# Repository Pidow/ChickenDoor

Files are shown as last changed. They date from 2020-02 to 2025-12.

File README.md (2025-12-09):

# ChickenDoor

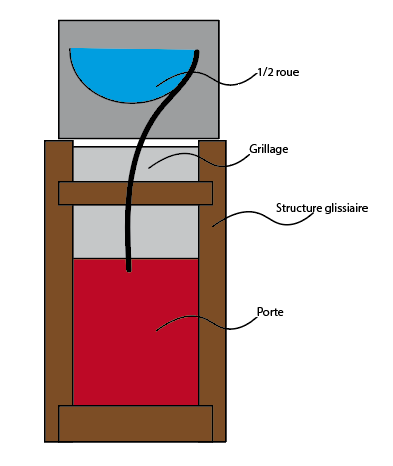
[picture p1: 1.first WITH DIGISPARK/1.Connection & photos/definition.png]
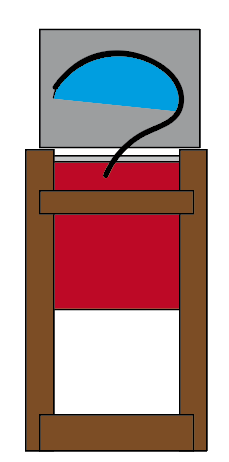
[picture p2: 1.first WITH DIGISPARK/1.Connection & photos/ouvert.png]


TARGET:
Move the chicken house doors 2 times per day.
Estimate battery lifetime: 8 month with AAA battery(x8).

### VERSION HISTORY
*   _[1st Version](https://github.com/Pidow/ChickenDoor/tree/master/1.first%20WITH%20DIGISPARK): Digispark STD with LED to have some information. Not very userfriendly. To add a screen we should use digispark pro._
*   _[2nd Version](https://github.com/Pidow/ChickenDoor/tree/master/2.Rebuild%20with%20DIGISPARK%20PRO): Digispark pro with screen (code not optimised)._
*   _[3st Version](https://github.com/Pidow/ChickenDoor/tree/master/3.With%20light%20sensor%20with%20DIGISPARK%20PRO): Digispark pro with screen and light sensor. After test, Tune the light sensor is very difficult, black cloud may close the door._
*   _[4th Version](https://github.com/Pidow/ChickenDoor/tree/master/4.Ephemeris%20version%20with%20DIGISPARK%20PRO): Actually the better version, base on south french Ephemeris. Code optimised, add watchdog sleep mode, add a push button to enter in debug mode and to wake up the screen._

## FOURTH VERSION DISGISPARK PRO VERSION & PUSH BUTTON: less 15€
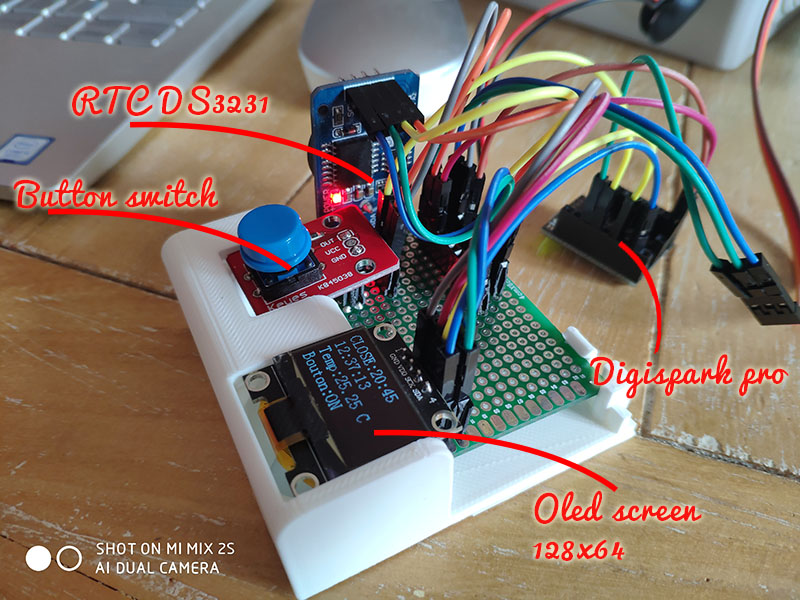
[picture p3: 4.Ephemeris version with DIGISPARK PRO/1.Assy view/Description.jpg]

*   ATTiny167 Digispark Pro
*   RTC DS3231 (Real Time clock)
*   Switch button
*   Battery holder 4 battery 1,5 v (x2)
*   Oled screen 128x64 I2C SPI serial.

## Description

Startup view.

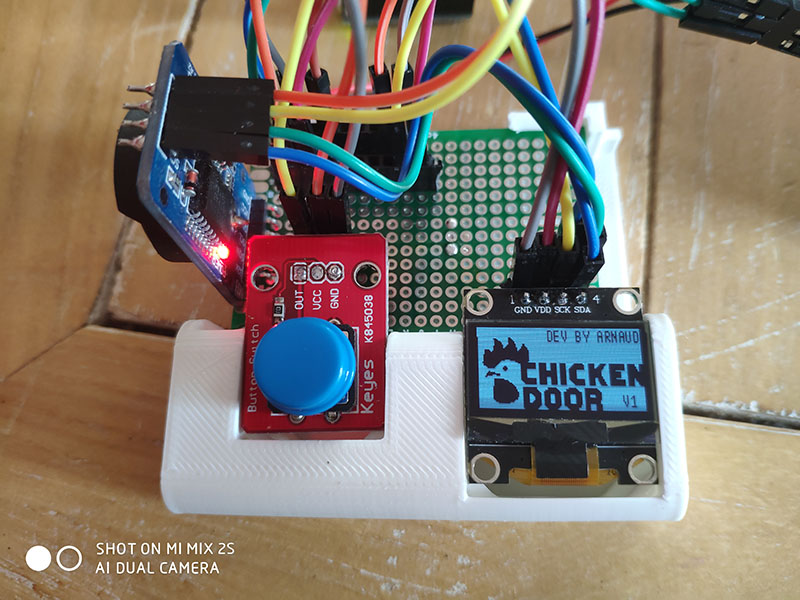
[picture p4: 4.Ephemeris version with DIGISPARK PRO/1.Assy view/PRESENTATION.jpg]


Press button after boot to enter in debug mode.
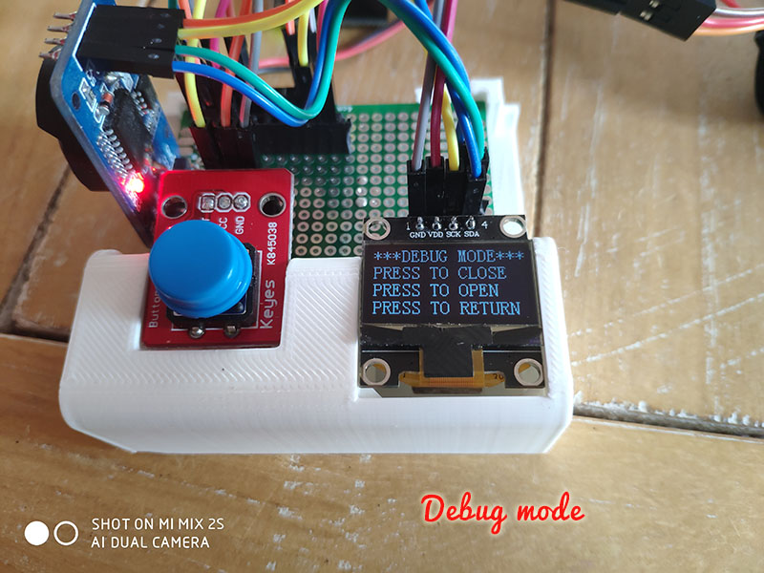
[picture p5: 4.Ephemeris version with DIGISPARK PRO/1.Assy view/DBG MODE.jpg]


Press 8secondes to wake up the screen when need. (screen shutdown after boot to reduce power consuming).
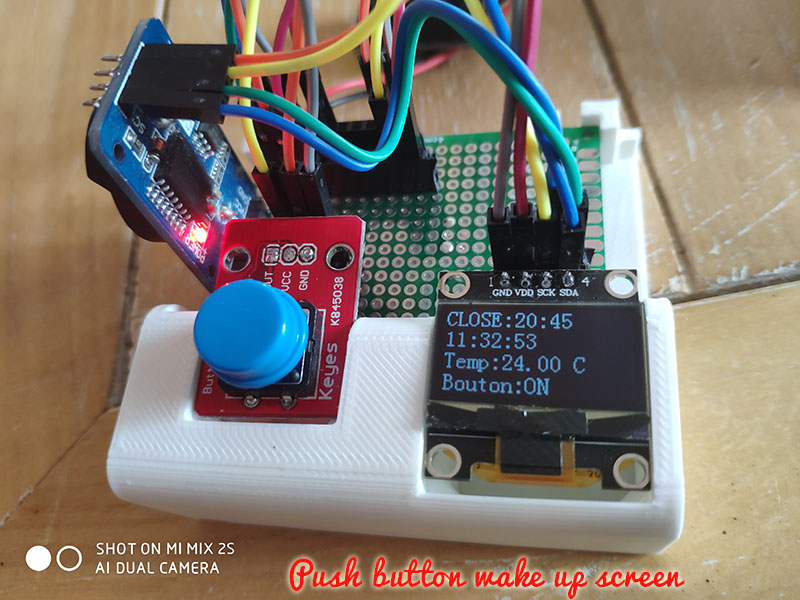
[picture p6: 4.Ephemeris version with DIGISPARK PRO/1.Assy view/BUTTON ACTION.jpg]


## CONNECTION
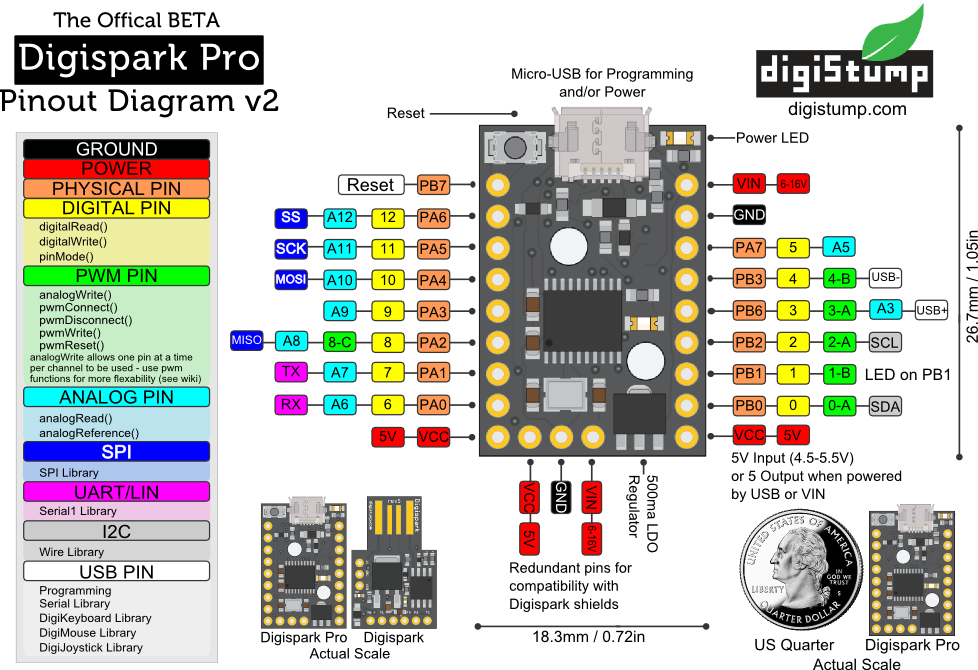
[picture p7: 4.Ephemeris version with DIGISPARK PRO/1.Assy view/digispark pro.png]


Connection for the digispark pro
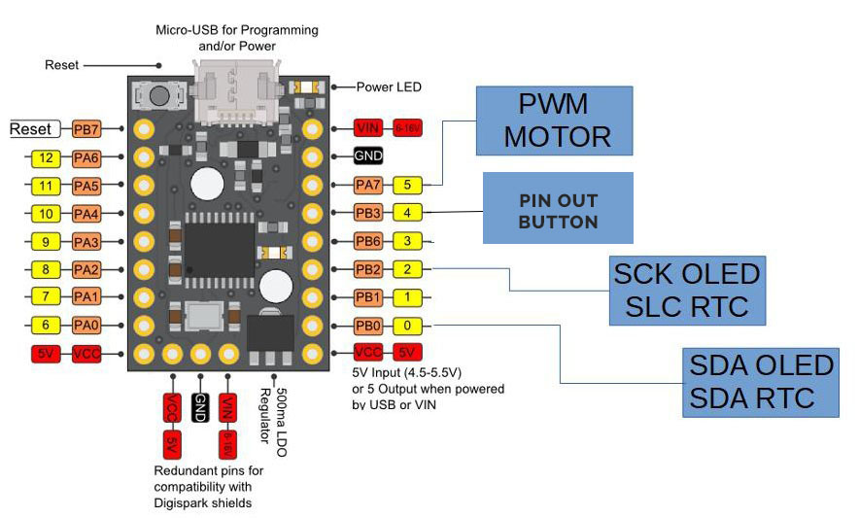
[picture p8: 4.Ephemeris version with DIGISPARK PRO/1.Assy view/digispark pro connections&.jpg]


Connection for the Servomotor MG995
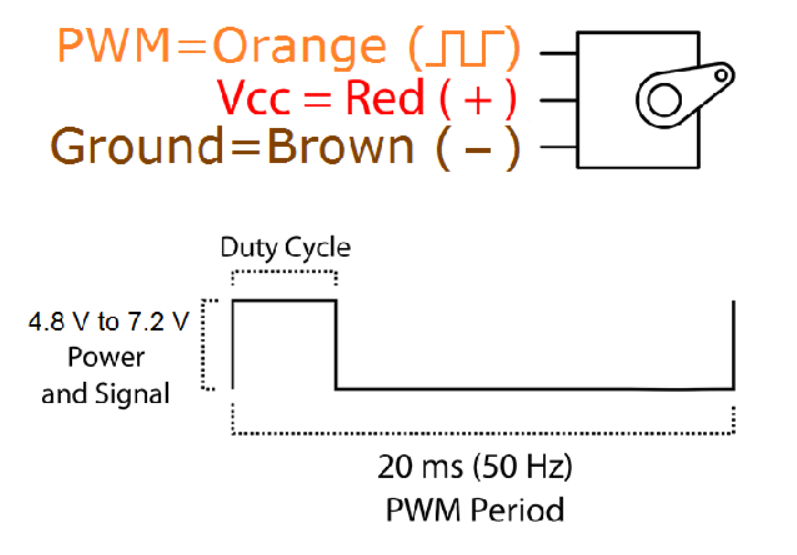
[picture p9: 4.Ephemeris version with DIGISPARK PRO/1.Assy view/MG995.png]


## 3D PRINT
Motor support:
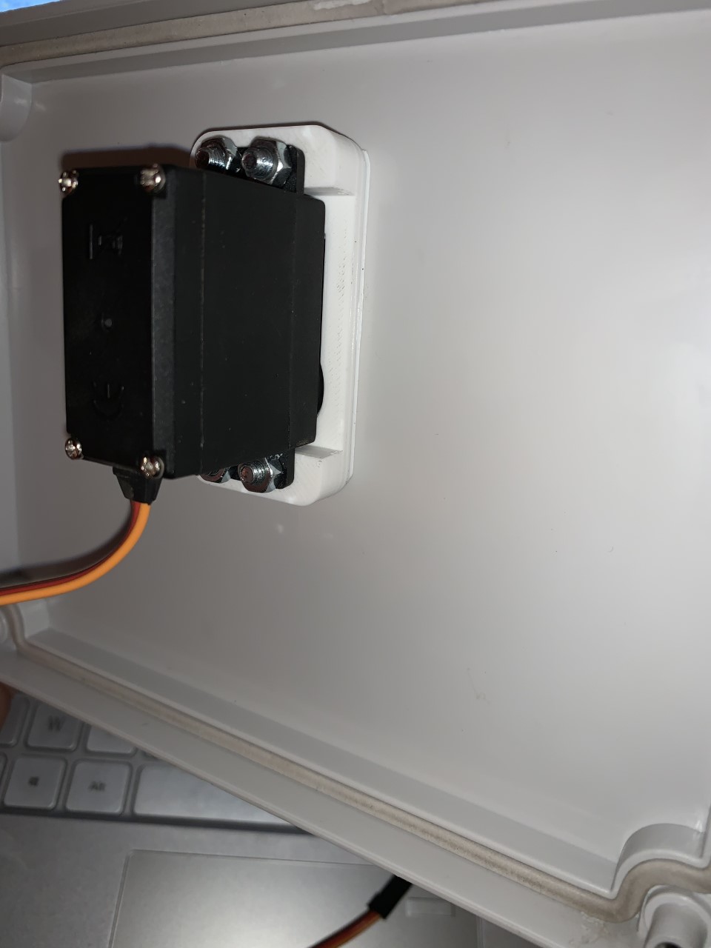
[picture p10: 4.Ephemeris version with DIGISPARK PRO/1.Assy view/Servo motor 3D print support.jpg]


1/2 wheel
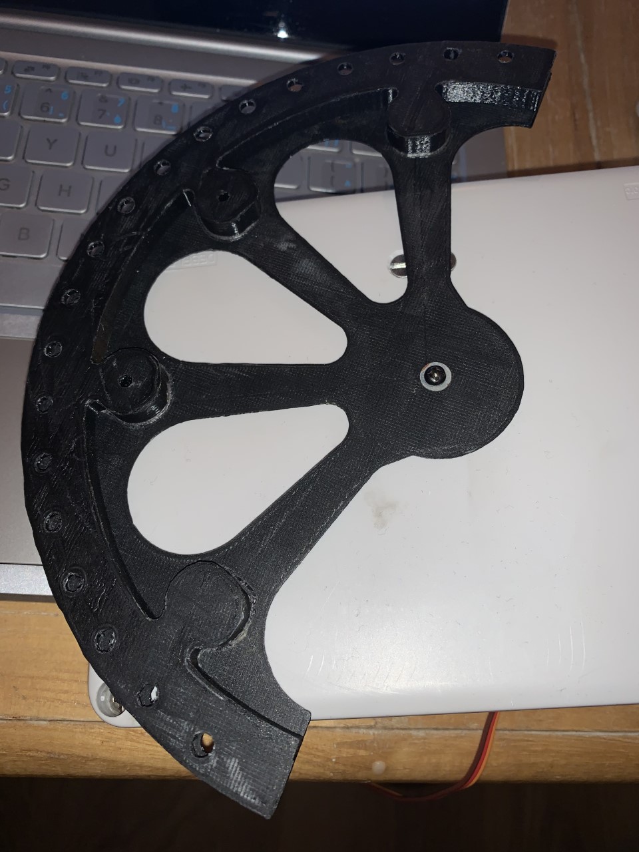
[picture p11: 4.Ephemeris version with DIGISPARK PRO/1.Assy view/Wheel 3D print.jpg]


## How it's work:
Push software to Digispark [following instruction](https://github.com/Pidow/ChickenDoor/blob/master/4.Ephemeris%20version%20with%20DIGISPARK%20PRO/3.Arduino%20code/Digispark%20arduino%20configuration.pdf), connect all component following instructions.
The system is ready !

Note:
If the RTC have power lost, software update it time automaticaly.
Oled screen & RTC use the same SDA and SCL connection to DIGISPARK.
RTC DS3231 allow to have Temp information.
I have put an relay to avoid battery consuming to maintain the servomotor position.
FYI Servomotor have only 180° angle, i have create a 3D print wheel to open the door.

> I'm available if any question.
> 
> Have fun !
> 
>    ARNAUD TOCABENS.
>
> https://tocabens.fr

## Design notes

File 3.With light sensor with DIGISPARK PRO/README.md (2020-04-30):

# ChickenDoor

SCREENLOGOSCREENLOGO

TARGET:
Move the chicken house doors 2 times per day.
Estimate battery lifetime: 8 month with AAA battery(x8).

## THIRD VERSION DISGISPARK PRO VERSION & LIGHT SENSOR cost: less 20€ 
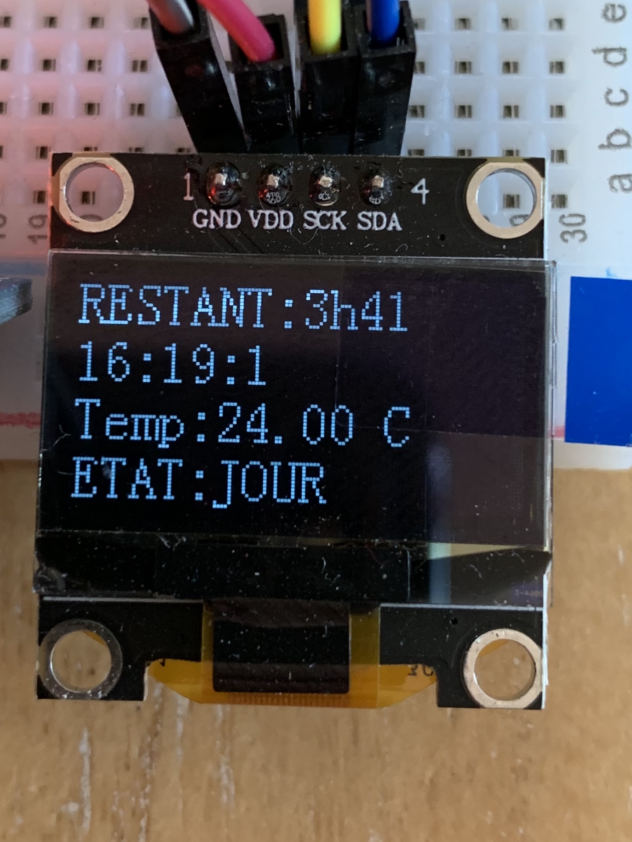
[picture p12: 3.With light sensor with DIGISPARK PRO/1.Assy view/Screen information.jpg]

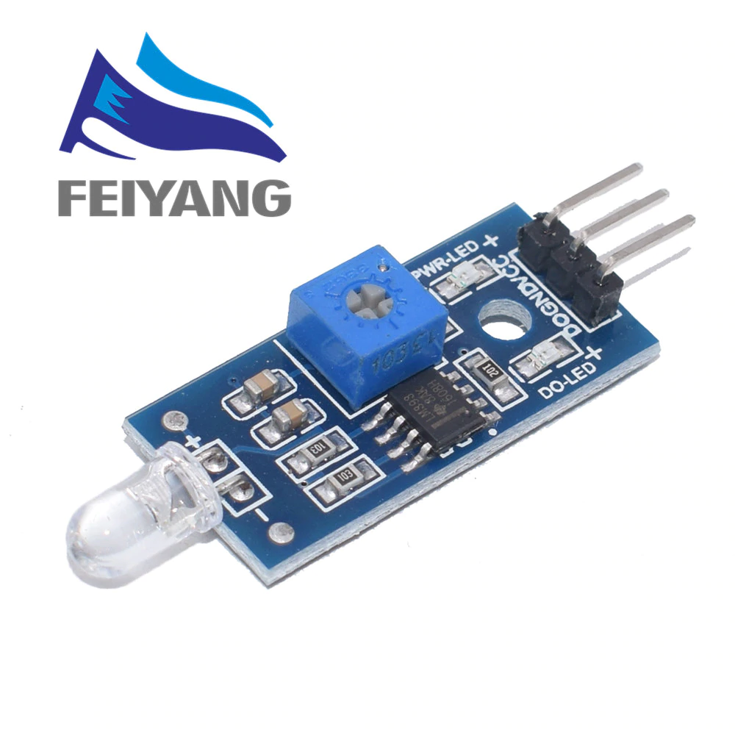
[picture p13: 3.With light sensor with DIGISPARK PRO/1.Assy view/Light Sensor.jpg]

*   ATTiny167 Digispark Pro
*   RTC DS3231 (Real Time clock)
*   Relay for Servomotor
*   Servomotor MG995
*   Battery holder 4 battery 1,5 v (x2)
*   Oled screen 128x64 I2C SPI serial.
*   Light Sensor

## CONNECTION
FIRSTVERSION
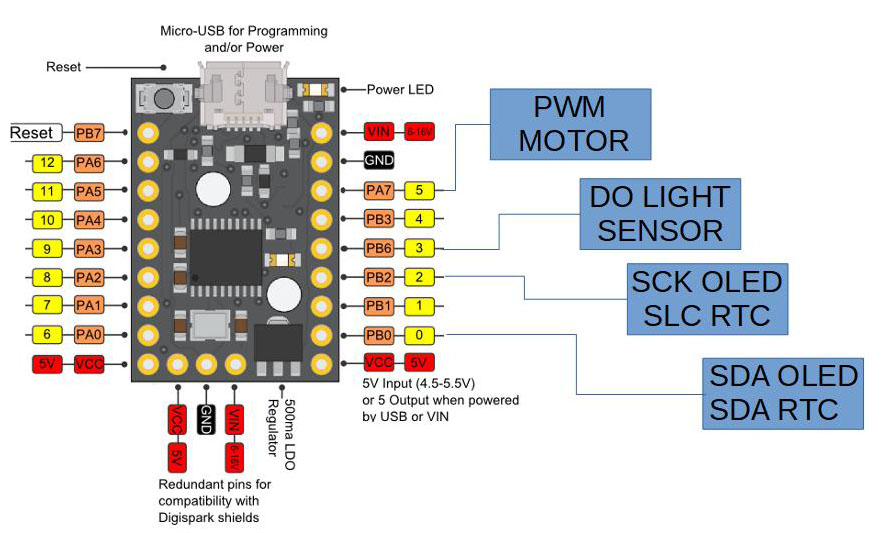
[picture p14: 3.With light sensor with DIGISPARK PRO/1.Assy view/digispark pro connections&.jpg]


```
How it's work:
Push software to Digispark, connect all component following instructions.
The system is ready !

Note:
If the RTC have power lost, software update it time automaticaly.
Oled screen & RTC use the same SDA and SCL connection to DIGISPARK.
RTC DS3231 allow to have Temp information.
I have put an relay to avoid battery consuming to maintain the servomotor position.
FYI Servomotor have only 180° angle, i have create a 3D print wheel to open the door.
```

> I'm available if any question.
> 
> Have fun !
> 
>    ARNAUD TOCABENS.

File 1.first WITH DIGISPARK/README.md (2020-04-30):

# ChickenDoor

SCREENLOGOSCREENLOGO

TARGET:
Move the chicken house doors 2 times per day.
Estimate battery lifetime: 8 month with AAA battery(x8).

## FIRST VERSION DIGISPARK STD VERSION cost: less 7€
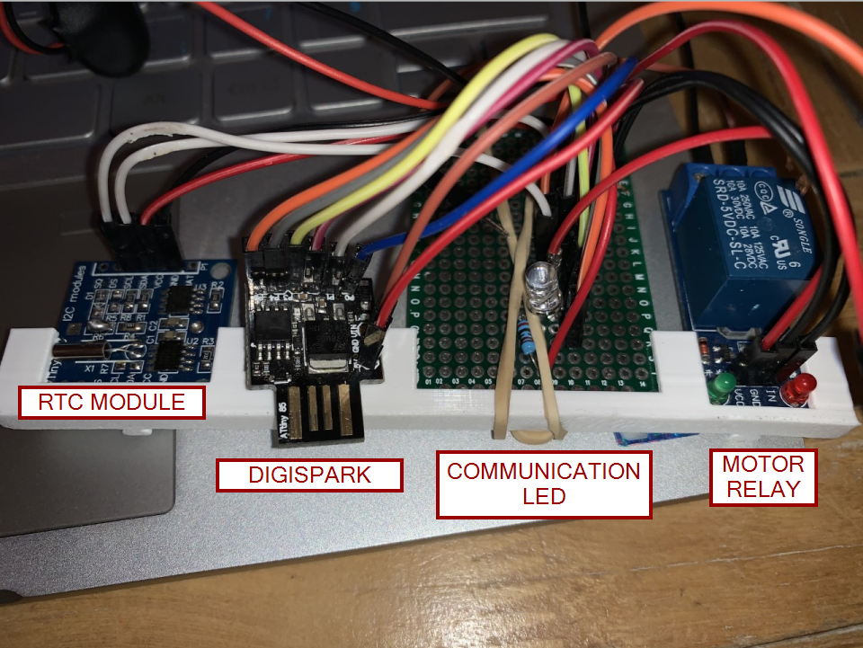
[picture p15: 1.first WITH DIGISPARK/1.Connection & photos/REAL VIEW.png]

*   ATTINY85 Digispark
*   RTC DS1307 (Real Time clock)
*   Relay for Servomotor
*   Servomotor MG995
*   Battery holder 4 battery 1,5 v (x2)
*   LED (to have some information

## CONNECTION
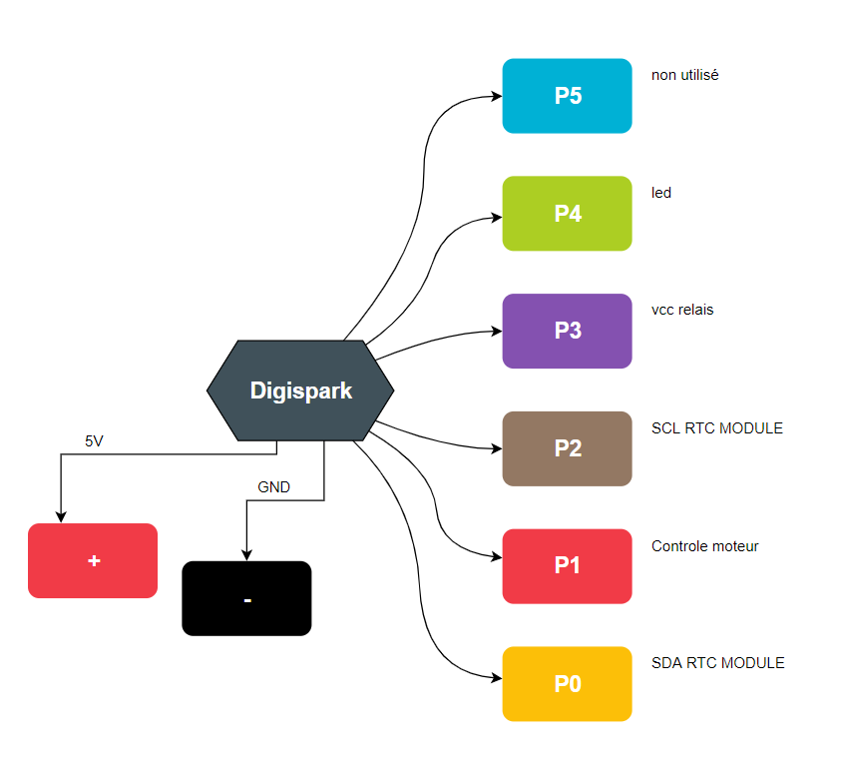
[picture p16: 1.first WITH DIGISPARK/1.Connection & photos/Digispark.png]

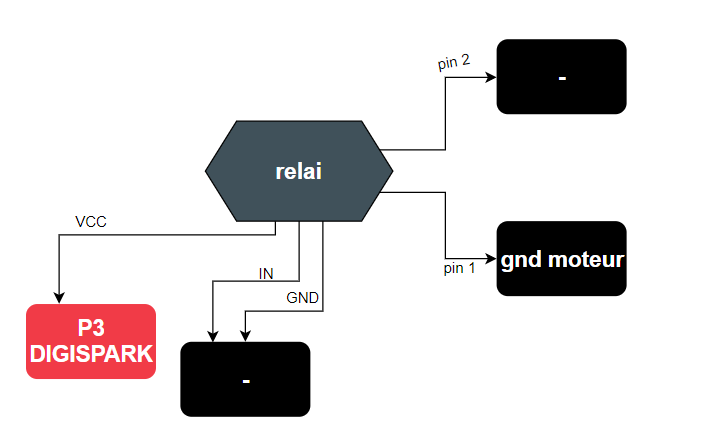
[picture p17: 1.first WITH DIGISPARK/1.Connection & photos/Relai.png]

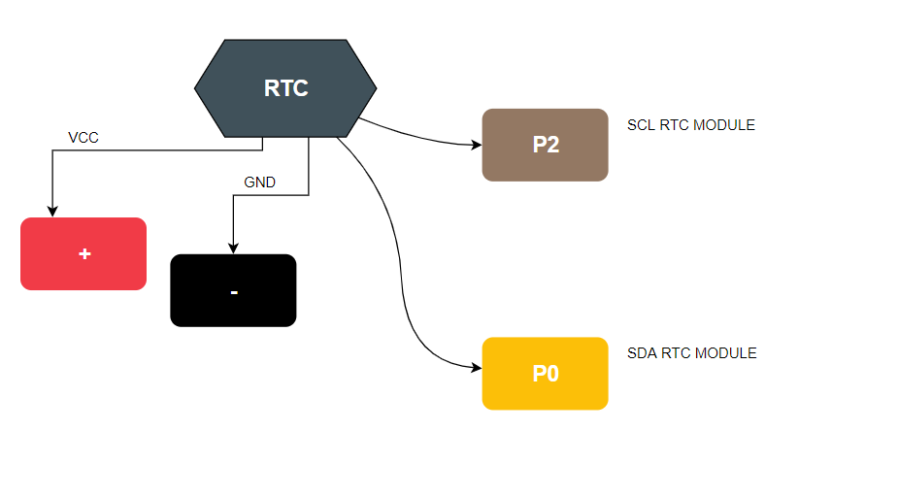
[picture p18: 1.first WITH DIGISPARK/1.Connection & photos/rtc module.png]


```
How it's work:
Push software to Digispark, connect all component following instructions.
The system is ready !

Note:
If the RTC have power lost, software update it time automaticaly.
Oled screen & RTC use the same SDA and SCL connection to DIGISPARK.
RTC DS3231 allow to have Temp information.
I have put an relay to avoid battery consuming to maintain the servomotor position.
FYI Servomotor have only 180° angle, i have create a 3D print wheel to open the door.
```

> I'm available if any question.
> 
> Have fun !
> 
>    ARNAUD TOCABENS.

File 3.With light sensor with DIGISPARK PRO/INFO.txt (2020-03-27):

For this version i have used:

ATTiny167 Digispark Pro
RTC DS3231 (Real Time clock)
Relay for Servomotor
Servomotor MG995
Battery holder 4 battery 1,5 v (x2)
Oled screen 128x64 I2C SPI serial.
SAMIORE ROBOT light sensor.

TARGET:
Move the chicken house doors 2 times per day.
Possible to connect the Oled screen sometimes to have information.
Estimate battery lifetime: 8 month with 2400mA battery.

How it's work:
Push software to Digispark.
If the RTC have power lost, software update it automaticaly.
Oled screen & RTC use the same SDA and SCL connection to DIGISPARK.
RTC DS3231 allow to have Temp information.
Light sensor must be adjusted on chickenhouse.

NOTE: Software is release, test is done.
But mounting test awaiting parts delivery.

You can use an relay to avoid battery consuming to maintain the servomotor position.
Becarefull Servomotor have only 180° angle, i have create a 3D print wheel to open the door.

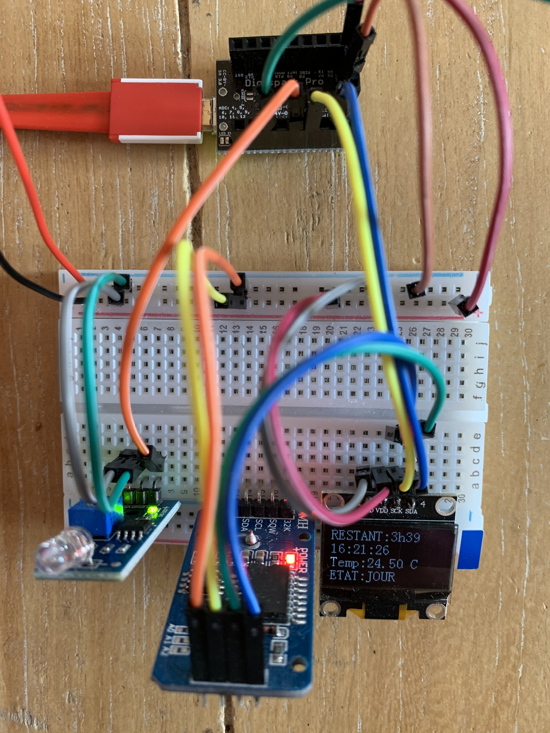
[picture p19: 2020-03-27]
3.With light sensor with DIGISPARK PRO/1.Assy view/Connection.jpg

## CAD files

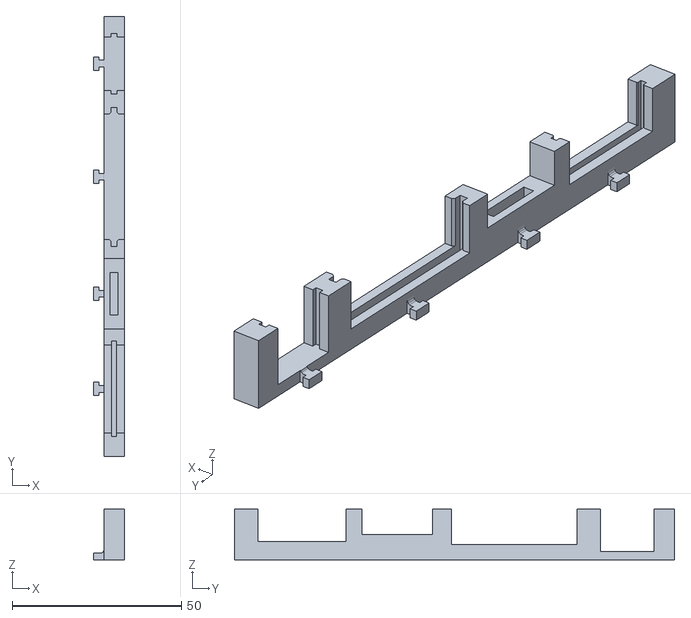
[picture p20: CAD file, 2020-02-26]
1.first WITH DIGISPARK/2. 3D print/SUPPORT PCB.stl
9.00 x 129.8 x 15.0

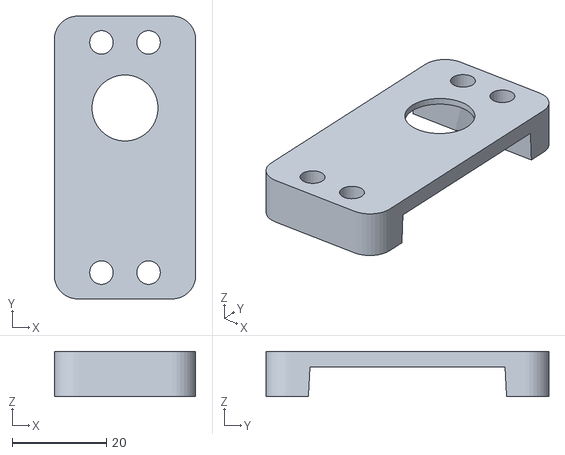
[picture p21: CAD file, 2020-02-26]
3.With light sensor with DIGISPARK PRO/2. 3D print/support moteur.stl
30.0 x 60.0 x 9.60

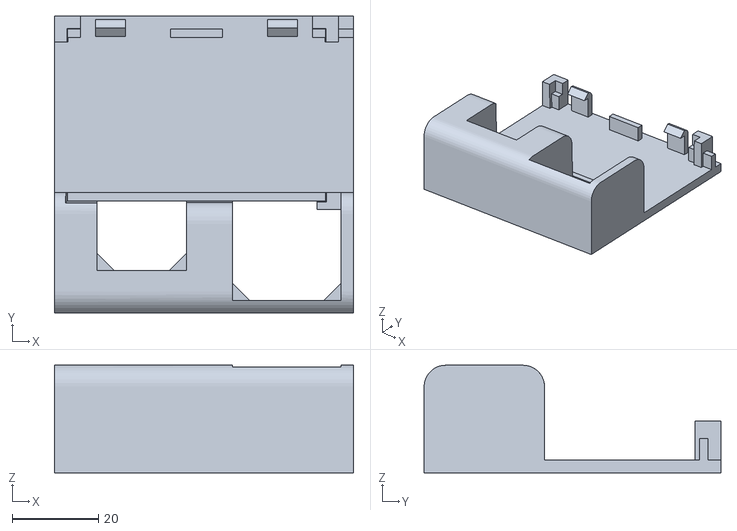
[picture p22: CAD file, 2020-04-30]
4.Ephemeris version with DIGISPARK PRO/2. 3D print/Support PCB NEW.stl
69.5 x 69.0 x 25.0

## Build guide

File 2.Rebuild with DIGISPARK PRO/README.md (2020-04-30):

# ChickenDoor

SCREENLOGOSCREENLOGO

TARGET:
Move the chicken house doors 2 times per day.
Estimate battery lifetime: 8 month with AAA battery(x8).

## SECOND VERSION DIGISPARK PRO VERSION cost: less 15€
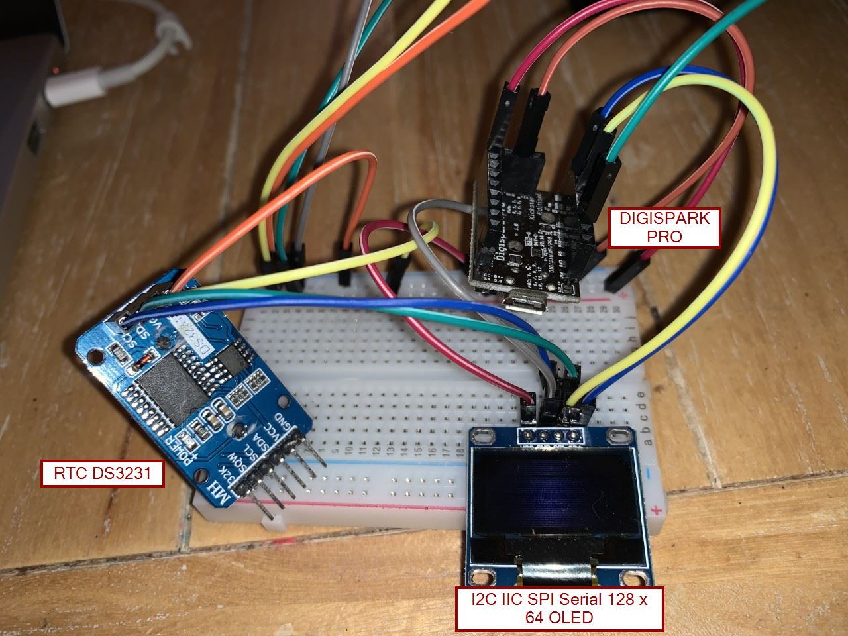
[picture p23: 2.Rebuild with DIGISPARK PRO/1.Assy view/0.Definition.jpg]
SECOND VERSION

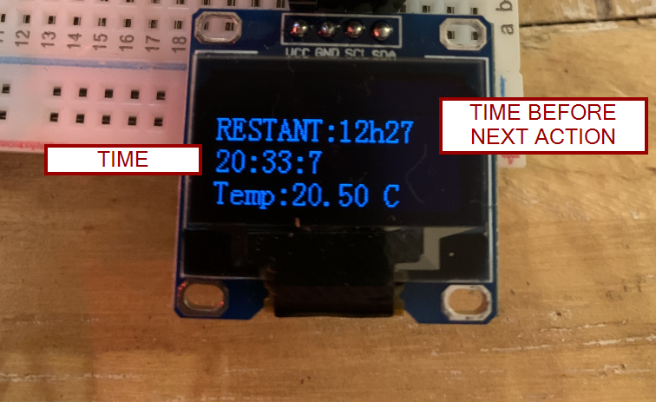
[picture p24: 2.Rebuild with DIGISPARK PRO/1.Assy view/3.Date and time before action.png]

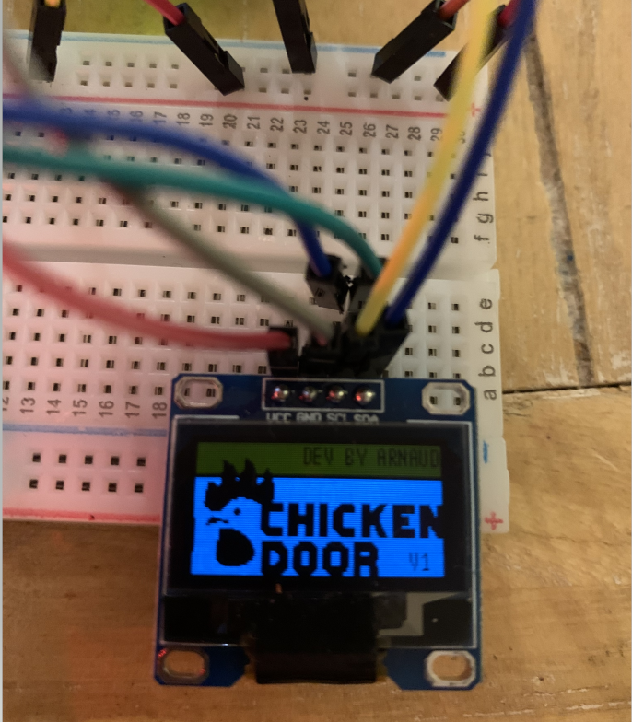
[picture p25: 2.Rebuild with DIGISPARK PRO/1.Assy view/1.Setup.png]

*   ATTiny167 Digispark Pro
*   RTC DS3231 (Real Time clock)
*   Relay for Servomotor
*   Servomotor MG995
*   Battery holder 4 battery 1,5 v (x2)
*   Oled screen 128x64 I2C SPI serial.

## CONNECTION
FIRSTVERSION
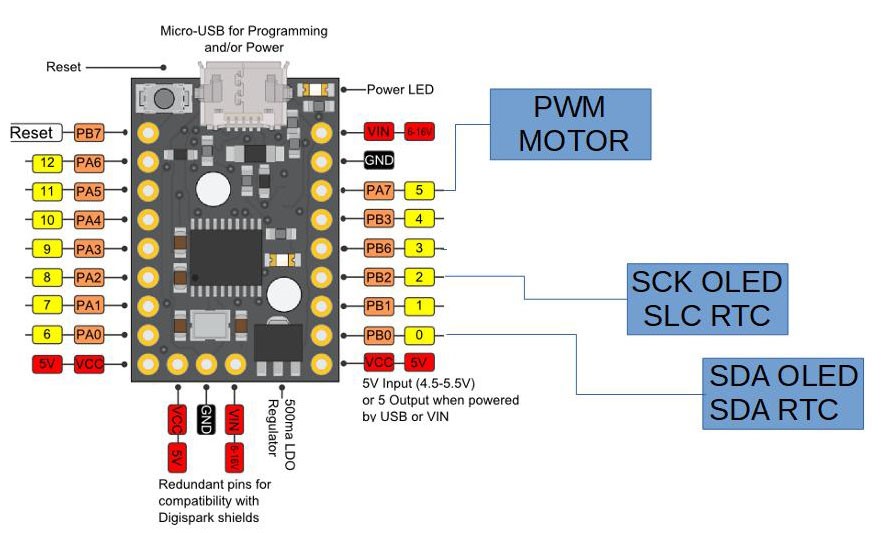
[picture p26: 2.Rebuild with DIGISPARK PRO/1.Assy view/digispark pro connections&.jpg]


```
How it's work:
Push software to Digispark, connect all component following instructions.
The system is ready !

Note:
If the RTC have power lost, software update it time automaticaly.
Oled screen & RTC use the same SDA and SCL connection to DIGISPARK.
RTC DS3231 allow to have Temp information.
I have put an relay to avoid battery consuming to maintain the servomotor position.
FYI Servomotor have only 180° angle, i have create a 3D print wheel to open the door.
```

> I'm available if any question.
> 
> Have fun !
> 
>    ARNAUD TOCABENS.

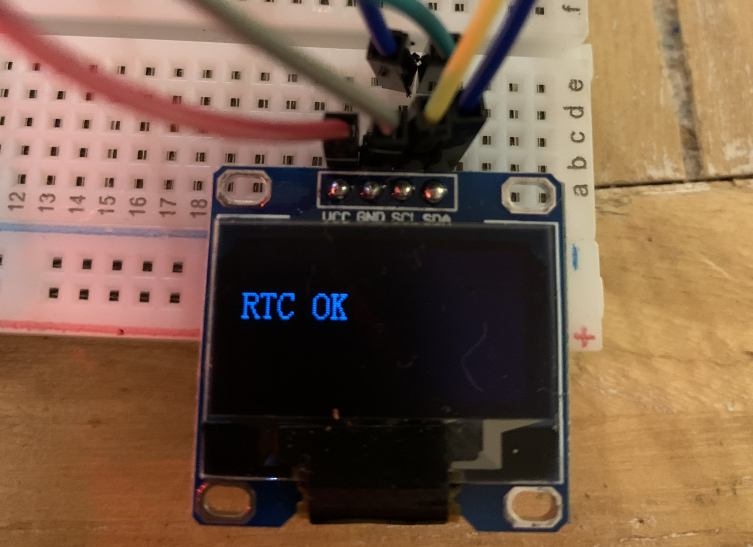
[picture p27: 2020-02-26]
2.Rebuild with DIGISPARK PRO/1.Assy view/2.RTC Check.png

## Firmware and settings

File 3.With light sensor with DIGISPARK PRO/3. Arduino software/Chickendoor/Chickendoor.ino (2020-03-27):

//***********SECTION ECRAN OLED*************
#include <DigisparkOLED.h>
#include <Wire.h>
#include "chickendoor_128x64c1.h"
//***********SECTION RTC DS3231 ************
#include "RTClib.h"
RTC_DS3231 rtc;
//***********SECTION SERVOMOTEUR ***********
  #include <SimpleServo.h>
  SimpleServo servo;
  
//***********VARIABLE**********************
int TSTART=10;//horaire ouverture par defaut
int TEND=20;//horaire fermeture par defaut
int TEMPSREST=0;//temps restant avant prochaine action.
long TEMPSRESTT=0;//millis temps delay avant control.
int MINREST=0;//minutes restant
bool PORTEOUV=0;//0:fermé - 1:ouvert
int sensorValue = 0; //Capteur solaire
bool DEBUG= 1;//mode test rafraichit l ecran tres regulierement.

//***********LANCEMENT PROG***************
void setup() {

//***********CAPTEUR LUMIERE***************
pinMode(3,INPUT);

//*******ACTIVATION MOTEUR +RELAIS *******
  //pinMode(3, OUTPUT); // moteur relai sur PIN 3
  pinMode(5, OUTPUT); //MOTEUR sur PIN5
  servo.attach(5);
  ouvrir(); //On ouvre la porte par defaut

  
//*******ACTIVATION ECRAN OLED *******
  oled.begin();
  oled.clear();
  oled.bitmap(0, 0, 128, 8, Chickendoorlogo);
  delay(8000);
  oled.clear();
  
//******VERIF RTC + MAJ *************  
    if (! rtc.begin()) {
        oled.println(F("Connection RTC Impossible"));
} else {
        if(DEBUG) {rtc.adjust(DateTime(F(__DATE__), F(__TIME__)));  };
        oled.setCursor(0, 2);
        oled.setFont(FONT8X16);
        oled.print(F("RTC OK"));
        if (rtc.lostPower()) {
                            oled.print(F("MISE A JOUR RTC OK !!"));
                            rtc.adjust(DateTime(F(__DATE__), F(__TIME__)));
                              }
        delay(1000);
		}
		
}
void loop() {
  sensorValue = digitalRead(3); // NUIT=1 JOUR=0
  DateTime now = rtc.now();
  if (now.hour() <  TSTART) { //AVANT HEURE CALCUL TEMPS AVANT OUVERTURE
							TEMPSREST=TSTART-now.hour();
							TEMPSRESTT=(((TEMPSREST-1)*60)+((60-now.minute()))*60000);
							MINREST=(60-now.minute());
							ecran();
							if( TEMPSRESTT >= 10800000) {
                            TEMPSRESTT=10800000;
                            }                                                            
                           if(!DEBUG) {delay (TEMPSRESTT);  };
							
  } else {      
        if ((TSTART == now.hour()) && (PORTEOUV == 0)) { //Heure ouverture
                            ouvrir();
		                        TEMPSRESTT=3660000;
		                        if(!DEBUG) {delay (TEMPSRESTT); };
        } else {
        if(( now.hour() > TSTART) && ( now.hour() < TEND)) {
                            TEMPSREST=TEND-now.hour();
                            TEMPSRESTT=(((TEMPSREST-1)*60)+((60-now.minute()))*60000);
							              MINREST=(60-now.minute());
							              ecran();
							              if( TEMPSRESTT >= 10800000) {
                              TEMPSRESTT=10800000;
                              }                                                            
                            if(!DEBUG) {delay (TEMPSRESTT); };
				} else {
       if ((TEND == now.hour()) && (PORTEOUV == 1)) {//Heure fermeture
							            if (!sensorValue) {//NUIT
							              fermer();
							              changh();
							              TEMPSRESTT=3660000;
                          } else {//Attente 10min
                            TEMPSRESTT=600000;
                          }
							            if(!DEBUG) {delay (TEMPSRESTT);	};

        } else {
        if ((now.hour() > TEND) && (PORTEOUV == 1)) { //au cas ou le delay depasse l'heure de fermeture peut importe etat lumiere ex panne
                          fermer();
                          changh();
                          TEMPSRESTT=3660000;
                          if(!DEBUG) {delay (TEMPSRESTT); };
                          
                          
        } else {
        if (now.hour() > TEND) {//APRES L'heure. calcul temps avant ouverture
                          TEMPSREST=(24-now.hour())+TSTART;
                          TEMPSRESTT=(((TEMPSREST-1)*60)+((60-now.minute()))*60000);
                          MINREST=(60-now.minute());
									        ecran();
									        if( TEMPSRESTT >= 10800000) {
									            TEMPSRESTT=10800000;
									            }                                                            
									        if(!DEBUG) {delay (TEMPSRESTT);};
													  }
									}
                }
    
              }
        }
}
}
void ouvrir() {
              digitalWrite(3, HIGH);
              delay(100);
              PORTEOUV=1;
              servo.write(180);
              delay(2000);
              digitalWrite(3, LOW);
              delay(100);              
              }
              
void fermer() {
              digitalWrite(3, HIGH);
              delay(100);
              PORTEOUV=0;
              servo.write(0);
              delay(2000);
              digitalWrite(3, LOW);
              delay(100);              
               }
			   
void ecran() {
  oled.begin();
  oled.clear();			
  

  //oled.setCursor(0, 2);
  oled.setFont(FONT8X16);
  
  //AFFICHE LE TEMPS RESTANT AVANT PROCHAINE ACTION
  oled.print(F("RESTANT:"));
  oled.print(TEMPSREST-1);
  oled.print(F("h"));    
  oled.print(MINREST);           
    oled.println();
 //AFFICHE L'heure actuelle
  DateTime now = rtc.now();
  oled.print(now.hour(), DEC);
  oled.print(F(":"));
  oled.print(now.minute(), DEC);
  oled.print(F(":"));
  oled.print(now.second(), DEC);
//AFFICHE LA TEMPERATURE
 oled.println();
 oled.print(F("Temp:"));
 oled.print(rtc.getTemperature());
 oled.print(F(" C"));
//AFFICHE LA VALEUR CAPTEUR SOLAIRE
  oled.println();
  oled.print(F("ETAT:"));
  if(sensorValue) {
       oled.print(F("NUIT"));
   } else  {
      oled.print(F("JOUR"));
  };
  //oled.print(sensorValue);
  
delay(1000);
}

void changh() {
   DateTime now = rtc.now();
  if(now.month() == 1) { 
                        TSTART=9;
                        TEND=18; 
                        }
  if(now.month() == 2) { 
                        TSTART=9;
                        TEND=19; 
                        }
  if(now.month() == 3) { 
                        TSTART=9;
                        TEND=20;//20h 
                        }
  if(now.month() == 4) { //+1h
                        TSTART=9;
                        TEND=21; 
                        }
  if(now.month() == 5) { 
                        TSTART=9;
                        TEND=22; 
                        }
  if(now.month() == 6) { 
                        TSTART=9;
                        TEND=22; 
                        }
  if(now.month() == 7) { 
                        TSTART=9;
                        TEND=22; 
                        }
  if(now.month() == 8) { 
                        TSTART=9;
                        TEND=22; 
                        }
  if(now.month() == 9) { 
                        TSTART=9;
                        TEND=21; 
                        }
  if(now.month() == 10) { 
                        TSTART=9;
                        TEND=19; 
                        }
  if(now.month() == 11) { //-1h
                        TSTART=9;
                        TEND=18; 
                        }
  if(now.month() == 12) { 
                        TSTART=9;
                        TEND=18; 
                        } 
}

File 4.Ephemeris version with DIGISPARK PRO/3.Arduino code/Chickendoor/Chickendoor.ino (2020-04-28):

//***********SECTION ECRAN OLED*************
#include <DigisparkOLED.h>
#include <Wire.h>
#include "chickendoor_128x64c1.h"

//***********WATCHDOG SLEEP MODE ***********
// using watch dog instead of delay
// Soft with delay: Power consumption: 0.108-0.120W
// Soft with Watchdog: Power Consumption: 0.038-0.051W
#include <avr/wdt.h>
#include <avr/sleep.h>
#include <avr/interrupt.h>
#define adc_disable() (ADCSRA &= ~(1<<ADEN)) // disable ADC (before power-off)
#define adc_enable()  (ADCSRA |=  (1<<ADEN)) // re-enable ADC

//***********SECTION RTC DS3231 ************
#include "RTClib.h"
RTC_DS3231 rtc;

//***********SECTION SERVOMOTEUR ***********
#include <SimpleServo.h>
SimpleServo servo;
  
//***********VARIABLE**********************
int TSTART=9;//horaire ouverture par defaut
int TEND=20;//horaire fermeture par defaut
int MEND=00;//Min fermeture par defaut
bool PORTEOUV=0;//0:fermé - 1:ouvert
bool TIME= 0;//Force MAJ RTC
int buttonState = 0; // BOUTON ON OU OFF. LOW= activé HIGH=non activé

//***********LANCEMENT PROG***************
void setup() {

//***********WATCH DOG ********************
  // Power Saving setup
  for (byte i = 0; i < 6; i++) {
    pinMode(i, INPUT);      // Met tous les ports en INPUT pour economiser l'energie
    digitalWrite (i, LOW);  //
  }
  adc_disable();          // Desactive le convertisseur Analog-to-Digital
  wdt_reset();            // RESET Watchdog
  wdt_enable(WDTO_8S);    // Temps du Watchdog: 15MS, 30MS, 60MS, 120MS, 250MS, 500MS, 1S, 2S, 4S, 8S
  WDTCR |= _BV(WDIE);     // Permettre l'interruption du watchdog.
  sei();                  // Permettre les interruptions
  set_sleep_mode(SLEEP_MODE_PWR_DOWN); // Sleep Mode: maximum

//*******ACTIVATION MOTEUR +RELAIS *******
  //pinMode(3, OUTPUT); // moteur relai sur PIN 3
  pinMode(5, OUTPUT); //MOTEUR sur PIN5
  servo.attach(5);
//*******BOUTON  ************************
pinMode(4, INPUT);

//*******ACTIVATION ECRAN OLED *******
  oled.begin();
  oled.clear();
  oled.bitmap(0, 0, 128, 8, Chickendoorlogo);
  delay(8000);
  oled.clear();
  
//******VERIF RTC + MAJ *************  
    if (! rtc.begin()) {
          oled.println(F("RTC CONNECT FAIL"));
      } else {
          if(TIME) {
         oled.print(F("DBG:RTC DONE !"));
         rtc.adjust(DateTime(F(__DATE__), F(__TIME__))); 
         delay(1000);
         };
          oled.setCursor(0, 2);
          oled.setFont(FONT8X16);
          oled.print(F("RTC OK"));
          if (rtc.lostPower()) {
                            oled.print(F("UPDATE RTC DONE!"));
                            rtc.adjust(DateTime(F(__DATE__), F(__TIME__)));
                              }
        delay(1000);
		}

//******DEBUG OPTION **************   
   oled.clear();
   oled.print(F("*PRESS TO DEBUG*"));
  // oled.println();
   //oled.print(F("1234567890123456"));
   delay (5000);
   buttonState = digitalRead(4);
   if (buttonState == LOW) {   
    oled.clear();
    dbg(); }//appui bouton 
    
   oled.clear();
   changh();
		
}
void loop() {
  DateTime now = rtc.now();
  buttonState = digitalRead(4);
  
if ((TSTART == now.hour()) && (PORTEOUV == 0)) { //Heure ouverture
                            ouvrir();
                            }
                                                
if ((TEND == now.hour()) && (MEND == now.minute()) && (PORTEOUV == 1)) {//Heure fermeture
                            fermer();
                            changh();
                            }
                              
if (buttonState == LOW) {   ecran(); //appui bouton
                            delay (10000);
                            oled.clear();
                            }  
attendre();                     
}

void attendre() {
                sleep_enable();
                sleep_cpu();
                }

ISR (WDT_vect) {
                WDTCR |= _BV(WDIE);
                }

void dbg() {
  oled.print(F("***DEBUG MODE***"));
  delay (3000);
  oled.println();
  oled.print(F("PRESS TO CLOSE"));
  buttonState = digitalRead(4); 
  while(buttonState == HIGH)  { buttonState = digitalRead(4); delay (100); }// si pas appui
  fermer();
  delay (3000);
  oled.println();
  oled.print(F("PRESS TO OPEN"));
  buttonState = digitalRead(4);   
  while(buttonState == HIGH)  { buttonState = digitalRead(4); delay (100); }// si pas appui
  ouvrir ();
  delay (3000);
  oled.println(); 
  oled.print(F("PRESS TO RETURN"));
  buttonState = digitalRead(4);
  while(buttonState == HIGH)  { buttonState = digitalRead(4); delay (100); }// si pas appui
  return;     
}

void ouvrir() {
              digitalWrite(3, HIGH);
              delay(100);
              PORTEOUV=1;
              servo.write(180);
              delay(2000);
              digitalWrite(3, LOW);
              delay(100);              
              }
              
void fermer() {
              digitalWrite(3, HIGH);
              delay(100);
              PORTEOUV=0;
              servo.write(0);
              delay(2000);
              digitalWrite(3, LOW);
              delay(100);              
               }
			   
void ecran() {
                DateTime now = rtc.now();
                oled.begin();
                oled.clear();			
                //oled.setCursor(0, 2);
                oled.setFont(FONT8X16);
  
  //AFFICHE LA PROCHAINE ACTION
                  oled.print(F("CLOSE:"));
                oled.print(TEND);
                oled.print(F(":"));
                oled.print(MEND);         
                oled.println();
                
 //AFFICHE L'heure actuelle
                oled.print(now.hour(), DEC);
                oled.print(F(":"));
                oled.print(now.minute(), DEC);
                oled.print(F(":"));
                oled.print(now.second(), DEC);
                
//AFFICHE LA TEMPERATURE
                oled.println();
                oled.print(F("Temp:"));
                oled.print(rtc.getTemperature());
                oled.print(F(" C"));

//ACTION BOUTON
             oled.println();
             oled.print(F("Bouton:"));
             if (buttonState == HIGH) {   oled.print(F("OFF")); } //OFF
             if (buttonState == LOW) {   oled.print(F("ON")); } //ON
                
  }

void changh() {
  DateTime now = rtc.now();

if(now.month() == 1) {
    if(now.day() < 9) {  TEND=17; MEND=30;  return;}
    if(now.day() < 20) {  TEND=17;  MEND=45;  return;}
    if(now.day() < 32) {  TEND=18;  MEND=00;  return;}
}

if(now.month() == 2) {
    if(now.day() < 12) {  TEND=18;  MEND=15;  return;}
    TEND=18;  MEND=30;  return;

}

if(now.month() == 3) {
    if(now.day() < 5) {  TEND=18; MEND=45;  return;}
    if(now.day() < 18) {  TEND=19;  MEND=00;  return;}
    if(now.day() < 30) {  TEND=19;  MEND=15;  return;}
    if(now.day() > 29) {  TEND=20;  MEND=15;  return;}
}

if(now.month() == 4) {
    if(now.day() < 12) {  TEND=20;  MEND=30;  return;}
    TEND=20;  MEND=45;  return;

}
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

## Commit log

2020-02-16 montage
    Digispark: http://digistump.com/products/1
    Relai: https://www.ebay.fr/itm/5V-Relay-Module-SRD-05VDC-SL-C-250V-125V-AC-30V-28V-DC-Arduino-Flux-Workshop-/111607485798
    RTC module: https://www.ebay.fr/i/322072366318?itemid=322072366318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
    Moteur type MG995.
2020-02-16 Programme arduino pour digispark
2020-02-16 Add files via upload
    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
2020-02-26 V6 update
    Update repository
    [SUPPORT PCB.stl, support moteur.stl]
2020-02-26 Add version with Digispark Pro
    Release soft for Digispark pro chicken door.
    [support moteur.stl]
2020-03-27 Add a new software
    New software with light sensor available.
    [support moteur.stl]
2020-03-27 Update with new version: Light sensor
2020-04-27 Create MG995.png
    Motor Connection information
2020-04-27 add a optimised version
    Add a new version version, without light sensor.
2020-04-28 Add a button
    Add a button to enter in debug mode or to shutdown the screen.
    Actually i use this version.
2020-04-30 update
    Update
    [Support PCB NEW.stl, support moteur.stl]
